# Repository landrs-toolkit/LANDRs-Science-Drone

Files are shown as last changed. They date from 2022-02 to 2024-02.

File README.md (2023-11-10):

# Nyala HexaQuad

<a href="https://github.com/landrs-toolkit/LANDRs-Science-Drone">
         
 </a>

LogoDiagram

**Welcome to the primary source for all the design materials and users guides for the LANDRS Nyala HexaQuad.**

The HexaQuad is an open source, modular multirotor designed with stringent academic research data provenance in mind.
It is a simple to replicate, user friendly design for drone novices and experts alike, all you need are some basic tools, a 3D printer and once off access to CNC routing.

**Specifications:**
* 15-20 minutes operation time with 1-3kg payload
* Configured as Hex or Quad
* Max flight time: 30 - 35 minutes (16.8Ah)
* Max Payload: 2kg(Quad); 5kg(Hex)
* Battery Voltage: 6S

A short description of the HexaQuad can be found on YouTube [here](https://youtu.be/huQ6nF6V_Ks) and detailed specifications can be seen below.

## Documentation

The documentation can be found at [https://www.landrs.org/LANDRs-Science-Drone/](https://www.landrs.org/LANDRs-Science-Drone/). This will house the build instructions, assistance guides and all information relating to the HexaQuad.

## Presentation at Linux Open Source Summit Europe 2022
We were invited to present our work at the Linux Open Source Summit that took place in Dublin, 2022. The Linux foundation flew us out to present our work to the open source community.

The full presentation given at the summit can be found on YouTube [here](https://youtu.be/drAO9xs3WeU).

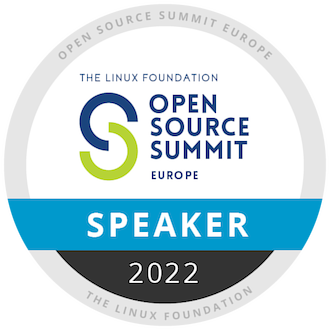
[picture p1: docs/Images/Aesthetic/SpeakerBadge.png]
LogoDiagram


In the presentation we explore the motivation for the HexaQuad and how it can benefit researchers compared to drones available off the shelf. There is further exploration of the design considerations and performance.

## License
Licensed under [CERN-OHL-P v2](https://cern.ch/cern-ohl) permissive variant or later.

## Citation
If using the work presented here, please use one of the following citation:

> **APA**: Borrageiro, M. G., & Wyngaard, J. Nyala HexaQuad, LANDRs' Science Drone (Version 1.0.0) [Designs]. https://github.com/landrs-toolkit/LANDRs-Science-Drone

> **BibTex**: @misc{Borrageiro_Nyala_HexaQuad_LANDRs,
author = {Borrageiro, Mauro Giovanni and Wyngaard, Jane},
title = {{Nyala HexaQuad, LANDRs' Science Drone}},
url = {https://github.com/landrs-toolkit/LANDRs-Science-Drone}
}

## Detailed Specifications:
| **Model** | **General** |
|---|---|
| Flight Controller | Cubepilot Orange Cube |
| Autopilot | Arducopter 4.3.1 |
| Navigation | Here 2 GPS |
| Remote Control | FrSky Archer GR8 ACCESS (Receiver), Taranis Q X7S (Transmitter) |
| Telemetry Radio | RFD900+ 900MHz radios |
| Operating Range (km) | 2 |
| Battery Voltage (V) | 22.2 (3.7x6) |
| Battery Capacity (Ah) | 8.4 - 16.8 |
| Motor | T-Motor MN5008 340KV 6S |
| Propeller | T-Motor P18x6.1 Carbon Fiber |
| Wingspan (mm) | 1120 (no props), 1578 (props on) |
| | **Hexacopter** |
| Configuration | Hex-X |
| Dimensions (W x L x H mm) | 1120 x 970 x 450 |
| Frame Weight (kg) | 2.7 |
| AUW, No battery (kg) | 3.7 |
| AUW(kg) | 4.6 - 5.5 |
| Max Thrust (N) | 246 |
| Max Payload (kg) | 5 |
| Typical Flight Time (1kg, min) | 28.8 |
| Maximum Flight Time (min) | 19.2 - 30.6 |
| | **Quadcopter** |
| Configuration | Quad-X |
| Dimensions (W x L x H mm) | 792 x 792 x 450 |
| Frame Weight (kg) | 2.2 |
| AUW, No battery (kg) | 2.9 |
| AUW(kg) | 3.8 - 4.6 |
| Max Thrust (N) | 165 |
| Max Payload (kg) | 2 |
| Maximum Flight Time, single battery (min) | 23 |

## Contact Details
You can connect with me on LinkedIn or via Email:

[Mauro-Borrageiro-87a5131b5](https://www.linkedin.com/in/mauro-borrageiro-87a5131b5/)

[mauro.borrageiro7@gmail.com](mauro.borrageiro7@gmail.com)

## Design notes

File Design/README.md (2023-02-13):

# Nyala HexaQuad Design Files

<a href="https://github.com/landrs-toolkit/LANDRs-Science-Drone/blob/main/docs/Images/Aesthetic/HexaQuadTracing.jpg">
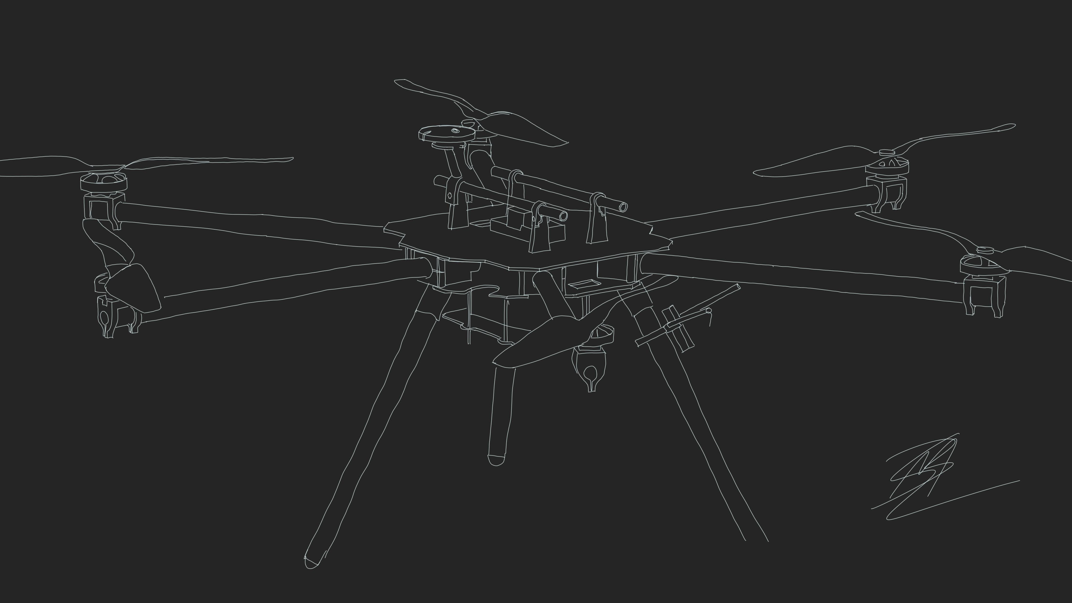
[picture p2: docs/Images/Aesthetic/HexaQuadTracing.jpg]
3DPrintBanner
         
 </a>

This folder contains all the mechanical 3D part files for the Nyala HexaQuad which can be editted and iterated. Included are the files for printing and CNC routing to recreate prototype 1 (Release 2022).

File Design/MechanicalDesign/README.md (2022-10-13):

# Mechanical Design Files for the LANDRs Science Drone

## Quad Configuration Part List:
*Note this is a minimal list and will be updated to the full requirements in November 2022*

| Part Name | Quantity | Manufacturing Technique |
|---|---|---|
| [BatteryPlate](https://github.com/landrs-toolkit/LANDRs-Science-Drone/tree/main/Design/MechanicalDesign/BatteryPlate) | 1 | CNC Carbon Fiber |
| [WingNutExtender](https://github.com/landrs-toolkit/LANDRs-Science-Drone/tree/main/Design/MechanicalDesign/BatteryPlate) | 4 | 3D Print |
| [CenterHub Top](https://github.com/landrs-toolkit/LANDRs-Science-Drone/tree/main/Design/MechanicalDesign/CenterHubs/TopPlate) | 1 | CNC Carbon Fiber |
| [CenterHub Bot](https://github.com/landrs-toolkit/LANDRs-Science-Drone/tree/main/Design/MechanicalDesign/CenterHubs/BottomPlate) | 1 | CNC Carbon Fiber |
| [LandingGearTubeCap](https://github.com/landrs-toolkit/LANDRs-Science-Drone/tree/main/Design/MechanicalDesign/LandingGear)  | 4 | 3D Print |
| [RotorBoomMounts Top](https://github.com/landrs-toolkit/LANDRs-Science-Drone/tree/main/Design/MechanicalDesign/RotorBoomMounts) | 4 | 3D Print |
| [RotorBoomMounts Bot](https://github.com/landrs-toolkit/LANDRs-Science-Drone/tree/main/Design/MechanicalDesign/RotorBoomMounts/NutInsert) | 4 | 3D Print |
| [MotorMounts](https://github.com/landrs-toolkit/LANDRs-Science-Drone/tree/main/Design/MechanicalDesign/MotorMounts) | 4 | 3D Print |
| [TopRail](https://github.com/landrs-toolkit/LANDRs-Science-Drone/tree/main/Design/MechanicalDesign/RailMounting) | 4 | 3D Print |
| [GPSMount](https://github.com/landrs-toolkit/LANDRs-Science-Drone/tree/main/Design/MechanicalDesign/GPSMounts) | 1 | 3D Print |
| [PDBMount](https://github.com/landrs-toolkit/LANDRs-Science-Drone/tree/main/Design/MechanicalDesign/PDBMount) | 1 | 3D Print |
| [NiTubeMounting](https://github.com/landrs-toolkit/LANDRs-Science-Drone/tree/main/Design/MechanicalDesign/SensorMounts/NiTubeMounting) | 2 | 3D Print |
| [RC Receiver](https://github.com/landrs-toolkit/LANDRs-Science-Drone/tree/main/Design/MechanicalDesign/RadioReceivers) | 1 | 3D Print |
| [Telemetry Radio](https://github.com/landrs-toolkit/LANDRs-Science-Drone/tree/main/Design/MechanicalDesign/RadioReceivers) | 1 | 3D Print |

## Print Guide
*For assistance with printing, please consult the HexaQuad dedicated documentation [here](https://www.landrs.org/LANDRs-Science-Drone/)*

- [Print Orientations](https://www.landrs.org/LANDRs-Science-Drone/GettingStarted/BuildInstructions/PrintGuide.html)
- [Nut Inserts](https://www.landrs.org/LANDRs-Science-Drone/GettingStarted/Tutorials/3DPrintInserts.html)

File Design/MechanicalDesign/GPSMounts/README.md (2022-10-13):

# GPS Mounting
This folder contians the development of the GPS mount. Two version were tested, a short and long option. The short mount is currently in use.

## All in One Mount
_This is the current prototype being used on both the Quad and Hex configuration of the multirotor._

<a href="https://github.com/landrs-toolkit/LANDRs-Science-Drone/blob/main/Design/MechanicalDesign/GPSMounts">
         
 </a>
<a href="https://github.com/landrs-toolkit/LANDRs-Science-Drone/blob/main/Design/MechanicalDesign/GPSMounts/Ai1HEREGpsMount.STL">
         
 </a>

This revision combined the rail mount and base plate into one single 3D print. Previously, these two components were seperate for ease of printing however,
 they were connected by a steel bolt. This was causing interference with the compass.
 
 There are two revisions of the Ai1HereGPSMount:
 - Ai1HereGpsMount (_Current Prototype (06/01/2022)_)
   - [STL File](https://github.com/landrs-toolkit/LANDRs-Science-Drone/blob/main/MechanicalDesign/GPSMounts/Ai1HEREGpsMount.STL), [SOLIDWORKS Part](https://github.com/landrs-toolkit/LANDRs-Science-Drone/blob/main/MechanicalDesign/GPSMounts/Ai1HEREGpsMount.SLDASM)
 - Ai1HereGpsMountLong
   - [STL File](https://github.com/landrs-toolkit/LANDRs-Science-Drone/blob/main/MechanicalDesign/GPSMounts/Ai1HEREGpsMountLong.STL), [SOLIDWORKS Part](https://github.com/landrs-toolkit/LANDRs-Science-Drone/blob/main/MechanicalDesign/GPSMounts/Ai1HEREGpsMountLong.SLDASM)
 
 The difference is a longer stem on the _long_ version to increase the height of the GPS from the center hub.

# Blank Designs for Customisation

## GPS Rail Mount
The GPS rail mount is still being used to connect the GPS to the top rails, it has simply been incorporated into a single 3D printed part in the Ai1HereGpsMount.

## HERE GPS
This was an attempt to create a snap-fit joint to hold he GPS in place. This is designed to work with the HERE GPS units, howevere requries some revision
and improvement to work as intended.

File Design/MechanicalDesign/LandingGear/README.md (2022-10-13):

# Landing Gear
This folder contains the current supported landing gear designs.

## Simple Tripod
<a href="https://github.com/landrs-toolkit/LANDRs-Science-Drone/tree/main/Design/MechanicalDesign/LandingGear/SimpleTripod">
         
 </a>
 <a href="https://github.com/landrs-toolkit/LANDRs-Science-Drone/blob/main/Design/MechanicalDesign/LandingGear/SimpleTripod/LGTubeCap.STL">
         
 </a>

This design makes use of simple tripod design for the landing gear. This steers away from the common 'T-Shaped' landing gear that has become synonymous with sUAS.
The Design is comprised of a carbon fiber tube which connects to the [Rotor Boom Mounts](https://github.com/landrs-toolkit/LANDRs-Science-Drone/tree/main/Design/MechanicalDesign/RotorBoomMounts) and has a simple rounded end that comes into contact 
with the floor. This is part is known as a [Landing Gear Tube Cap](https://github.com/landrs-toolkit/LANDRs-Science-Drone/tree/main/Design/MechanicalDesign/LandingGear/SimpleTripod) and is 3D printed.

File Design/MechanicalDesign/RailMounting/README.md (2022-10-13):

# Gimbal Rail Mounts
This folder contains the mounts to support the top and bottom gimbal rails. Both rails are a 250mm long carbon fiber tube with a 12mm diameter.

## Top Gimbal Rail Mount:
<a href="https://github.com/landrs-toolkit/LANDRs-Science-Drone/blob/main/Design/MechanicalDesign/RailMounting/TopRail/PrtTopGimbalNutInsert.STL">
         
 </a>
<a href="https://www.landrs.org/LANDRs-Science-Drone/GettingStarted/Tutorials/3DPrintInserts.html">
         
 </a>

This folder contains the top gimbal rail mounting part. Included is a PDF drawing with dimentions to aid with custom mounting. [Top Rail](https://github.com/landrs-toolkit/LANDRs-Science-Drone/tree/main/Design/MechanicalDesign/RailMounting/TopRail)

## Bottom Gimbal Rail Mount:
<a href="https://github.com/landrs-toolkit/LANDRs-Science-Drone/tree/main/Design/MechanicalDesign/RailMounting/BotRail/TRodGimbalMountNutInsert.STL">
         
 </a>
<a href="https://www.landrs.org/LANDRs-Science-Drone/GettingStarted/Tutorials/3DPrintInserts.html">
         
 </a>

This folder contains the bottom gimbal rail mounting part. Included is a PDF drawing with dimentions to aid with custom mounting. [Bot Rail](https://github.com/landrs-toolkit/LANDRs-Science-Drone/tree/main/Design/MechanicalDesign/RailMounting/TopRail)

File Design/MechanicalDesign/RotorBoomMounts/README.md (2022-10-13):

# Rotorboom Mounts

The Rotorboom Mounts assist in two ways, firstly to connect the rotorbooms (arms) of the HexaQuad to the central hub of the drone. Secondly, they provide an attachment point for the landing gear to the central hub.

Thus there are two configurations this doc covers: a rotorboom mount that accommodates the landing gear and the rotorboom; and a configuration that accommodates the rotorboom only.

# Mounts Differences

## Top Rotorboom Mount
<a href="https://github.com/landrs-toolkit/LANDRs-Science-Drone/blob/main/Design/MechanicalDesign/RotorBoomMounts/NutInsert/LGLegMountTopV3.2NutInsert.STL">
         
 </a>
 <a href="https://www.landrs.org/LANDRs-Science-Drone/GettingStarted/Tutorials/3DPrintInserts.html">
         
 </a>

The top mount is used in both configurations, that accommodating the landing gear and the rotorboom only.

## Bottom Rotorboom Mount

<a href="https://github.com/landrs-toolkit/LANDRs-Science-Drone/blob/main/Design/MechanicalDesign/RotorBoomMounts/LGLegMountBotV3.1.STL">
         
 </a>

The bottom mount is used only in the case when landing gear is required to be attached to the rotorboom.

# Configurations

## Rotorboom Only
This configuration onlt requires the top mount.

**Required 3D prints:**

- 2 x [LGLegTopMount](https://github.com/landrs-toolkit/LANDRs-Science-Drone/blob/main/Design/MechanicalDesign/RotorBoomMounts/NutInsert/LGLegMountTopV3.2NutInsert.STL)

**Illustration:**

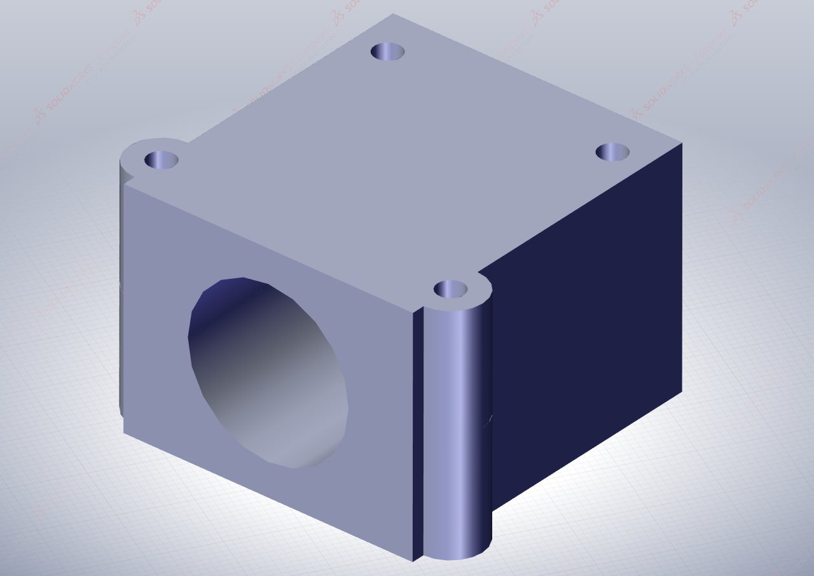
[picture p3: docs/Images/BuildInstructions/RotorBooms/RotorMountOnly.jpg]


## Rotorboom and Landing Gear

This configuration makes use of both the top and bottom mounts.

**Required 3D prints:**

- 1 x [LGLegTopMount](https://github.com/landrs-toolkit/LANDRs-Science-Drone/blob/main/Design/MechanicalDesign/RotorBoomMounts/NutInsert/LGLegMountTopV3.2NutInsert.STL)
- 1 x [LGLegBotMount](https://github.com/landrs-toolkit/LANDRs-Science-Drone/blob/main/Design/MechanicalDesign/RotorBoomMounts/LGLegMountBotV3.1.STL)

**Illustration:**

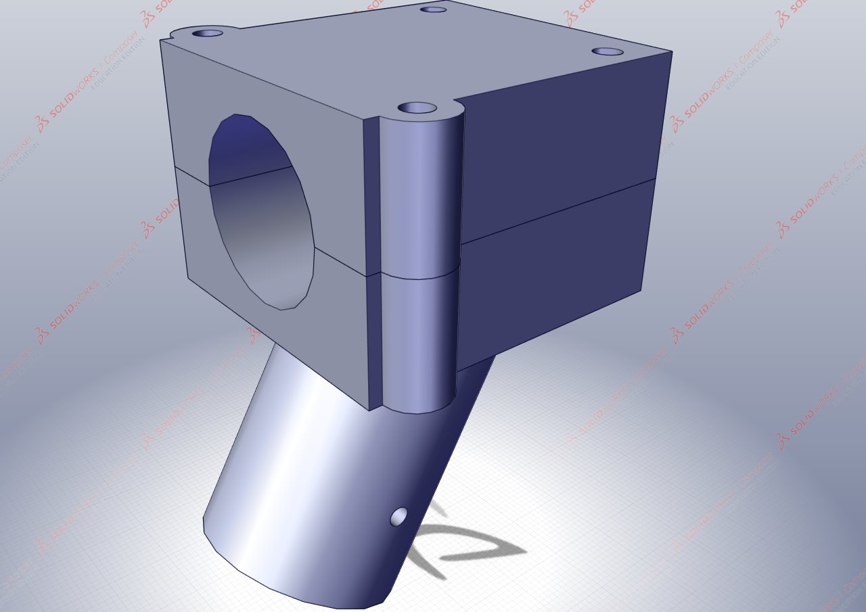
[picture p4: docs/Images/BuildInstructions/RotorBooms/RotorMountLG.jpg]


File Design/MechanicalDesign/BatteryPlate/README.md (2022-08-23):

# Battery Mounting
This repositorty contains the battery mounting plate that connects to the center hub. This design is being prototyped and is likely to have some minor updates to improve operation.

## Battery Plate with Butterfly Nut

<a href="https://github.com/landrs-toolkit/LANDRs-Science-Drone/blob/main/Design/MechanicalDesign/BatteryPlate">
         
 </a>
<a href="https://github.com/landrs-toolkit/LANDRs-Science-Drone/blob/main/Design/MechanicalDesign/BatteryPlate/BatPlateBtFlyNut.DXF">
         
 </a>

The contents of the folder:

**BatPlateButFlyNut.SLDPRT**:
- SOLIDWORKS, 3D editable part file of the battery mounting plate secured with butterfly nuts.

**BatPlateButFlyNut.DXF**:
- CNC Cutting/Routing file for the battery plate.
- The material used in the prototype was Carbon Fiber Twill Weave, 3mm thickness.

**WingNutExtender.SLDPRT**

<a href="https://github.com/landrs-toolkit/LANDRs-Science-Drone/blob/main/Design/MechanicalDesign/BatteryPlate/WingNutExtender.SLT">
         
 </a>
 <a href="https://www.landrs.org/LANDRs-Science-Drone/GettingStarted/Tutorials/3DPrintInserts.html">
         
 </a>

- SOLIDWORKS, 3D editable part file for a printable wingnut to assist with securing the battery. This part requires an embedded M5 nut.

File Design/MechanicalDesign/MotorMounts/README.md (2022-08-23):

# 3D Printed Motor Mounts
The Science Drone is making use of 3D printed motor mounts. Motor mounts can often be complex shapes and thus make the manufacturing process somewhat difficult and long. 3D printing fixes this problem and shortens the manufacturing process.

There was a concern of strength of the 3D printed materials. Thus a Tensile loading test was performed on two materials to investigate if either would be sufficient for the purpose. Both materials proved suitable interms of strength however, concerns of temperature and melting points of the materials was raised. PETG has a higher melt temperature compared to PLA and this partially motivated the comparison between the two materials. Fortunately, it was found during testing that the motor operating temperatures were not a concern and thus the material with a higher tensile strength was used, PLA.

The Motor Mount went through three significant design iterations and are listed below.
The folder contains 3D `.STL` files for printing and `.SLDPRT` SOLIDWORKS editable part files

 <a href="https://github.com/landrs-toolkit/LANDRs-Science-Drone/blob/main/Design/MechanicalDesign/MotorMounts/MMPrintV1.3c.STL">
         
 </a>
 
## MotorMount Print (MMPrint):
-  A simple design with a single securing point to mount the motor to the rotor boom.

**Design Concerns:**
1.   The mount had to be aligned to the end of the rotor boom and then also leveled. 
2.   If the single securing point came undone or failed, then the motor would certainly fall off and cause more damage.

These issues were revised in iteration 2.

## MMPrintV1.2:
- Iteration 2 saw the addition of an end stopper plate to help align the motor mount with the end of the rotor boom. 
- There was also an additional securing point for redundancy but also to further secure the motor mount to the rotor boom.

**Design Concerns:**
1. The design of the securing point was a point subject to high strain when loaded to fasten the mount to the rotor boom. Due to the sharp corner and contant width, this resulted in a high stress point and broke under loading.
2. The tolerance of the rotorboom hole was upped by 0.3mm to account for the error in 3D printing. [ID change: 25mm->25.3mm]

## MMPrintV1.3:
- Iteration 3 introduced more tolerance in the diameters to account for 3D printing error. 
- A Fillet was added to the design to distribute the stress more evenly along the securing point.
- The thickness of the mount was increased by 1mm as a precaution and avoid another iteration.
- Added a angled slot to accommodate the motor wires. This allows the wires to go further into the rotor boom instead of being exteranl to the boom.

**Design Concerns:**
1. The bottom of the motor shaft seems to be touching the top of the motor mount, adding friction and making it more difficult to turn the motor. [Proposed to add a cut out for clearance]

## MMPrintV1.4:
<a href="https://github.com/landrs-toolkit/LANDRs-Science-Drone/blob/main/Design/MechanicalDesign/MotorMounts">
         
 </a>

- Added a clearance cut to the surface where the motor shaft was touching.

**Design Notes:**
The concern raised in the previous version was proved true. The bottom of the motor shafts were rubbing on the 3D print, wearing away the material. The clearance was added as a precaution to prevent unnecessary added friction on the motor shafts.

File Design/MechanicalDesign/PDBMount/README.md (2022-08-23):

# Power Distribution Board (PDB) Mount:
<a href="https://github.com/landrs-toolkit/LANDRs-Science-Drone/blob/main/Design/MechanicalDesign/PDBMount/PDBMount.STL">
         
 </a>
 <a href="https://www.landrs.org/LANDRs-Science-Drone/GettingStarted/Tutorials/3DPrintInserts.html">
         
 </a>

The PDB mount is designed for the [Matek PDB-HEX, 12S](https://www.mateksys.com/?portfolio=pdb-hex) board. The simple mount is to secure the PDB and provide some electrical isolation of the PCB from the carbon fiber center plate. 

The design mirrors the shape of the PCB and has embedded nuts to secure the PDB to the mount. The PDB is currently secured to the center hub with industrial velcro.

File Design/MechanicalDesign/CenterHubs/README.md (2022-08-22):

# Modular Chassis Unit (MCU) Designs
This folder contains the part and CNC routing files for the Top and Bottom plates of the centeral hub.

Simulation studies were performed on the centeral hub designs listed below. The simulation studies were instrumental in determining which set of plates would best suit the applications of the multirotor.

## DoDeca Chassis Unit, Design 1
The DoDeca design is based off a polygon with 12 sides (a dodecagon). 
This number of sides allowed for a satisfying mounting configuration of the rotors booms for both a quad and hex configuration. 
12 sides mean that in either a quad or hex configuration the rotor booms would always be perpendicular to a chassis edge.

This is a simple design and increases in surface area equally in all directions. Weight minimizing cutouts can be added in to imporve weight to strength performance.

## Oblong Chassis Unit, Design 2
The Oblong design is a more rectangular based design where the majority of the surface area is focused along one axis. 
The resulting shape is a chassis plate extending longer in one axis compared to its relative perpendicular axis. An example can be seen in the following figure:


## Double Plate Unit, Design 3
<a href="https://github.com/landrs-toolkit/LANDRs-Science-Drone/blob/main/Design/MechanicalDesign/CenterHubs">
         
 </a>

The following ietration builds on the ideas in the previous versions. This design contains a top and bottom plate that "sandwiches" the Rotor-leg mounts for added support and structural strength. The bottom plate has various cutouts to accommodate the reconfiguration between Hex and Quad, leading to the interchangable HexaQuad.

**CHObDoubleTop:** 
- Top plate of the central hub.

**CHDoDeDoubleBot:** 
- Bottom plate of the central hub.

### Version 1.2

The files for version 1.2 can be found in the following folders:
- [TopPlate](https://github.com/landrs-toolkit/LANDRs-Science-Drone/tree/main/Design/MechanicalDesign/CenterHubs/TopPlate)
- [BottomPlate](https://github.com/landrs-toolkit/LANDRs-Science-Drone/tree/main/Design/MechanicalDesign/CenterHubs/BottomPlate)

Each folder contains an editable 3D SOLIDWORKS file and a non-editable DXF file used for CNC cutting/routing of the plates.

### Visual Representation Only:
[This folder](https://github.com/MBorrageiro/cad-drawings/tree/main/CenterHub/MCUDesigns/STLs) contains STL files of certain assemblies and parts just to serve as a visual representation. It is not the intention for these parts to be 3D printed.

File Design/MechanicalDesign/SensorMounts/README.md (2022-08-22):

# Sensor Mounts and Related Items
*Under development...*

This folder contains parts to assist with mounting sensors to the HexaQuad. It also provides solutions for mounting items associated with sensors such as Type-C USB sockets for powering devices.

## Type-C Socket Mounts:
Some suggested and tested mounting strategies for USB Type-C sockets for powering devices. [Type-C Mounts](https://github.com/landrs-toolkit/LANDRs-Science-Drone/tree/main/Design/MechanicalDesign/SensorMounts/C-TypeSocketMounts)

## Nut Insert (Ni) Tube Mounting:
A simple mount that fits onto any 25mm diameter carbon tube of the HexaQuad. This is used for mounting the RFD telemetry radios and R/C receiver. [Ni-Tube Mount](https://github.com/landrs-toolkit/LANDRs-Science-Drone/tree/main/Design/MechanicalDesign/SensorMounts/NiTubeMounting)

## Nut Insert (Ni) Rail Mounting:
A simple mount to aid connection to the gimbal rails. This part has a 12mm diameter and can be used on either the top or bot gimbal rail. [Ni-Rail Mount](https://github.com/landrs-toolkit/LANDRs-Science-Drone/tree/main/Design/MechanicalDesign/SensorMounts/NutInsertRailMounting)

## Rail Snap On Mounts:
A horrizontal bar that 'snap-locks' onto the parallel 12mm gimbal rails. There are two lengths available due to different spacings of the top and bot gimbal rails. [SnO Mounts](https://github.com/landrs-toolkit/LANDRs-Science-Drone/tree/main/Design/MechanicalDesign/SensorMounts/RailSnapMount)

## Rail Mounting Blanks:
This folder contains blank models of the GPS rail mount and gimbal rail mounts. These blanks can be merged with custom sensor mounts to connect them to the HexaQuad. [Rail Mounting Blanks](https://github.com/landrs-toolkit/LANDRs-Science-Drone/tree/main/Design/MechanicalDesign/SensorMounts/RailMountingBlanks)

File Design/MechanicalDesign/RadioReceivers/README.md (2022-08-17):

# Radio Receiver Mounts
This folder contains mounting designs for the radio controller (R/C) and the telemetry recievers. These mounts are not strickly necessary and can be replaced with 3M or other adhessive options, however this is not recommended.

## RC Reciever:
 <a href="https://github.com/landrs-toolkit/LANDRs-Science-Drone/blob/main/Design/MechanicalDesign/RadioReceivers/RCReceiver">
         
 </a>

The R/C designs are specificly for the FrSky ARCHER GR8 Receiver.
There are two designs inlcuded, where the antenna are oriented 90&deg; apart, just in two different planes. This snap fit makes use of the following [carbon fiber tube mount](https://github.com/landrs-toolkit/LANDRs-Science-Drone/tree/main/Design/MechanicalDesign/SensorMounts/NiTubeMounting)

**90VP:**

The antenna are 90&deg; apart in the vertical plane(VP). One runs vertically and the other horizontally.

**90HP:**

This differs to the VP in that both antenna are in the horizotnal plane(HP), yet still 90&deg; apart.

## Telemetry Radios.
 <a href="https://github.com/landrs-toolkit/LANDRs-Science-Drone/blob/main/Design/MechanicalDesign/RadioReceivers/TelemetryRadios">
         
 </a>

The HexaQuad has two options for telemetry links, one makes use of RFD900 radios and the second, is based on a mobile network. The telemetry links are the main connection between the HexaQuad and the ground control station(GCS). The suggested mounting options are listed below:

### RFD900 Mounts:
There are two differnet 3D printable cases, one that allows mounting of the receiver on the HexaQuad and another that serves as a protective case of the transmitter that connects to the GCS.

**Telemetry Case for HexaQuad:**

A simple snap fit case to protect the RFD telemetry radio and provide a mounting point to secure the radio to the HexaQuad. This snap fit makes use of the following [carbon fiber tube mount](https://github.com/landrs-toolkit/LANDRs-Science-Drone/tree/main/Design/MechanicalDesign/SensorMounts/NiTubeMounting)

[STL Files](https://github.com/landrs-toolkit/LANDRs-Science-Drone/blob/main/Design/MechanicalDesign/RadioReceivers/TelemetryRadios)

**Telemetry Case for GCS:**

*Coming soon...*

## 5G Mobile Network Mounts:
*Coming soon...*

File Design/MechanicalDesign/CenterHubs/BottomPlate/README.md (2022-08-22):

# Center Hub Dodecagon Bottom Plate
<a href="https://github.com/landrs-toolkit/LANDRs-Science-Drone/blob/main/Design/MechanicalDesign/CenterHubs/BottomPlate/CHDoDeDoubleBotV1.2.DXF">
         
 </a>

The bottom plate of the LANDRs Hex and Quad drone. The plate has universal cuts that allow the sUAS to be changed between a hexacopter or a quadcopter.

This folder contains the following files:

**CHDoDeDoubleBotV1.2.SLDPRT:**
- Solidworks Editable 3D file.
- The dimensions of the plate can be altered or features can be added or removed.

**CHDoDeDoubleBotV1.2.DXF:**
- The DXF file is used for CNC cutting of the plate.

NOTE: It is recommended to use the Solidworks Part File to export the part to different formats if required.

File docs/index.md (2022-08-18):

---
layout: default
title: Home
nav_order: 1
---

# Nyala HexaQuad Documentation
Welcome to the "landing ;)" page of the HexaQuad, LANDRs Modular Science Multicopter.
This is the home of the NyHQ's Documentation and will guide you through assembly, debugging and hopefully some customisation. 



<a href="https://github.com/landrs-toolkit/LANDRs-Science-Drone/blob/main/docs/Images/Aesthetic/HexaQuadTracing.jpg">
         3DPrintBanner
 </a>

**Status:**
* The HexaQuad is undergoing performance testing, see provisional flight performance [here](https://youtu.be/huQ6nF6V_Ks)
* Repo currently primarily contains CAD Drawings related to the 3D printable parts and CNC'd parts.
* This repo intends to release version 1 before the end of 2022

**License**
Licensed under [CERN-OHL-P v2](https://cern.ch/cern-ohl) permissive bariant or later.

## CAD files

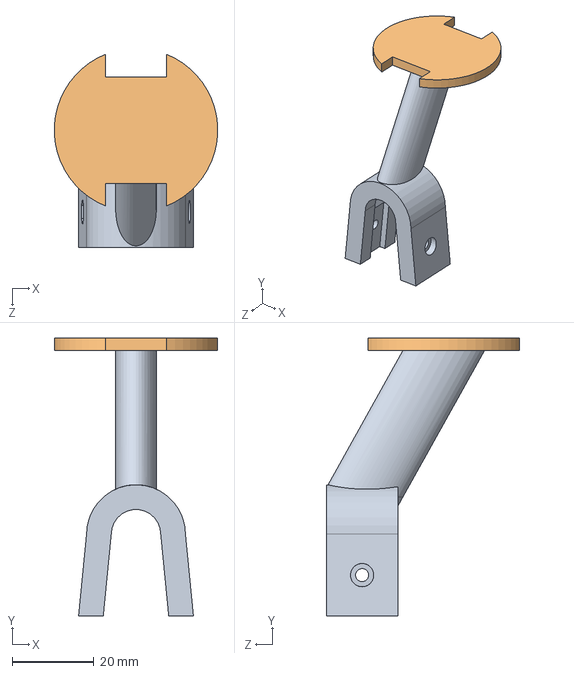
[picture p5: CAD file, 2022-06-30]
Design/MechanicalDesign/GPSMounts/Ai1HEREGpsMount.SLDASM
39.9 x 68.0 x 47.3 mm
GpsRailMount
HEREGpsBSimple

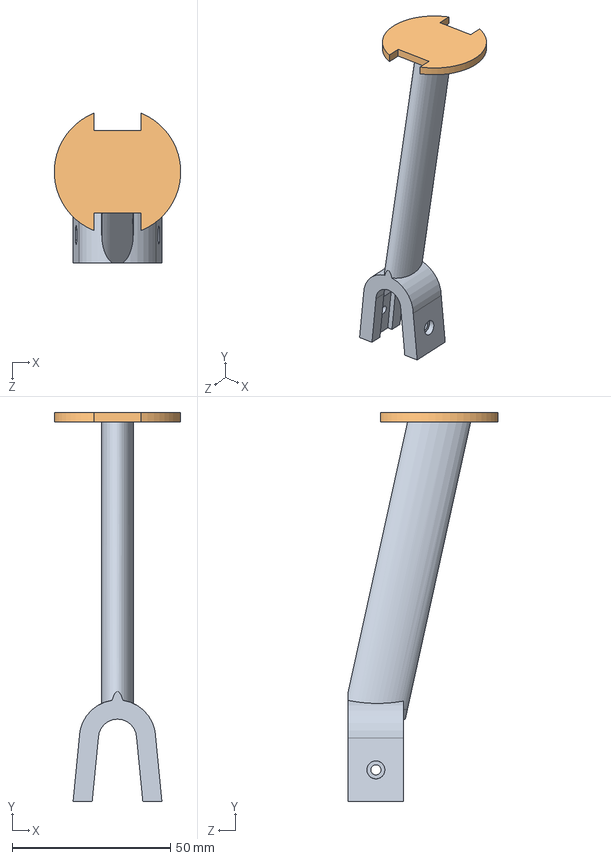
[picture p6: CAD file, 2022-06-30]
Design/MechanicalDesign/GPSMounts/Ai1HEREGpsMountLong.SLDASM
39.9 x 123.0 x 47.3 mm
GpsRailMountLong
HEREGpsBSimple

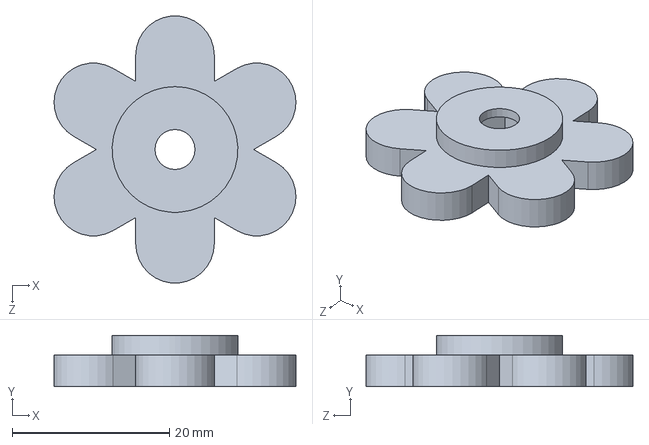
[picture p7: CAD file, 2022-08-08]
Design/MechanicalDesign/BatteryPlate/WingNutExtender.SLDPRT
30.8 x 6.50 x 33.9 mm

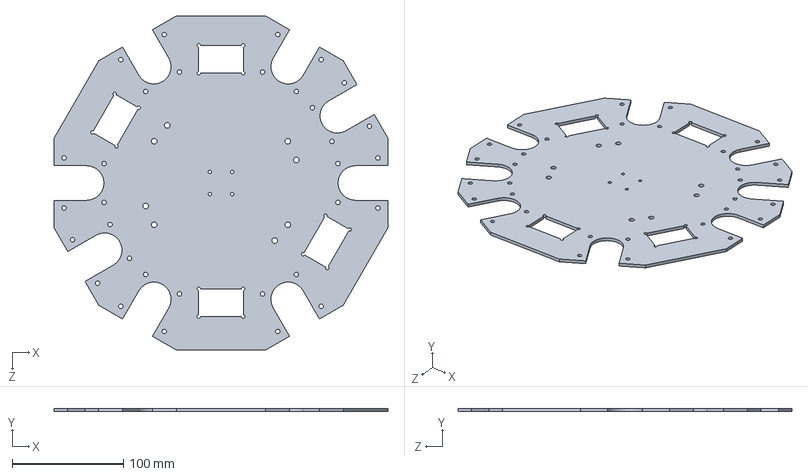
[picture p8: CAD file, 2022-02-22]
Design/MechanicalDesign/CenterHubs/BottomPlate/CHDoDeDoubleBotV1.2.SLDPRT
300.0 x 3.00 x 300.0 mm

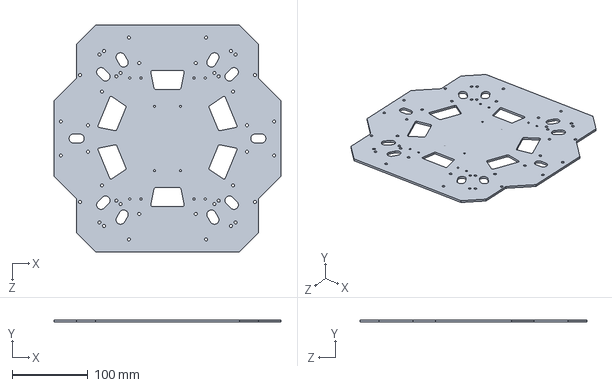
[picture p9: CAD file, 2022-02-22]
Design/MechanicalDesign/CenterHubs/TopPlate/CHObDoubleTopV1.2.SLDPRT
300.0 x 3.00 x 300.0 mm

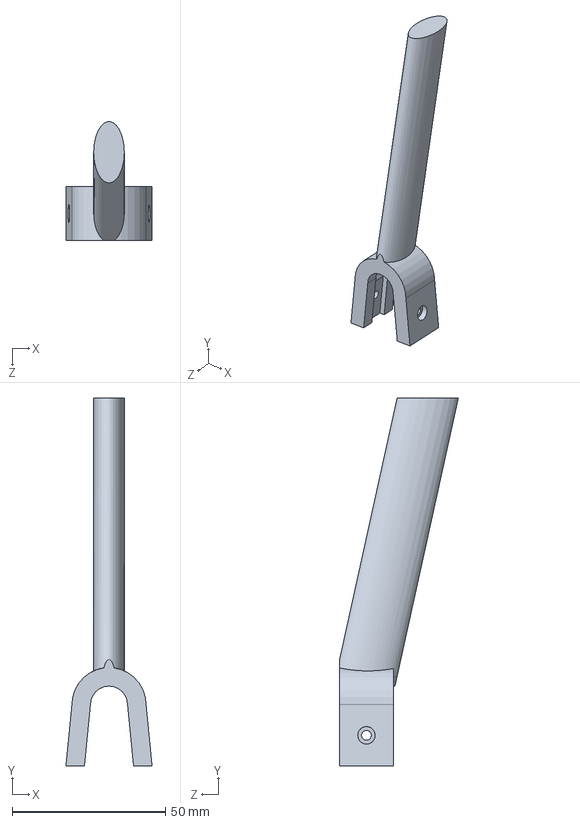
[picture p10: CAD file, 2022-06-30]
Design/MechanicalDesign/GPSMounts/GpsRailMount.SLDPRT
28.1 x 120.0 x 38.7 mm

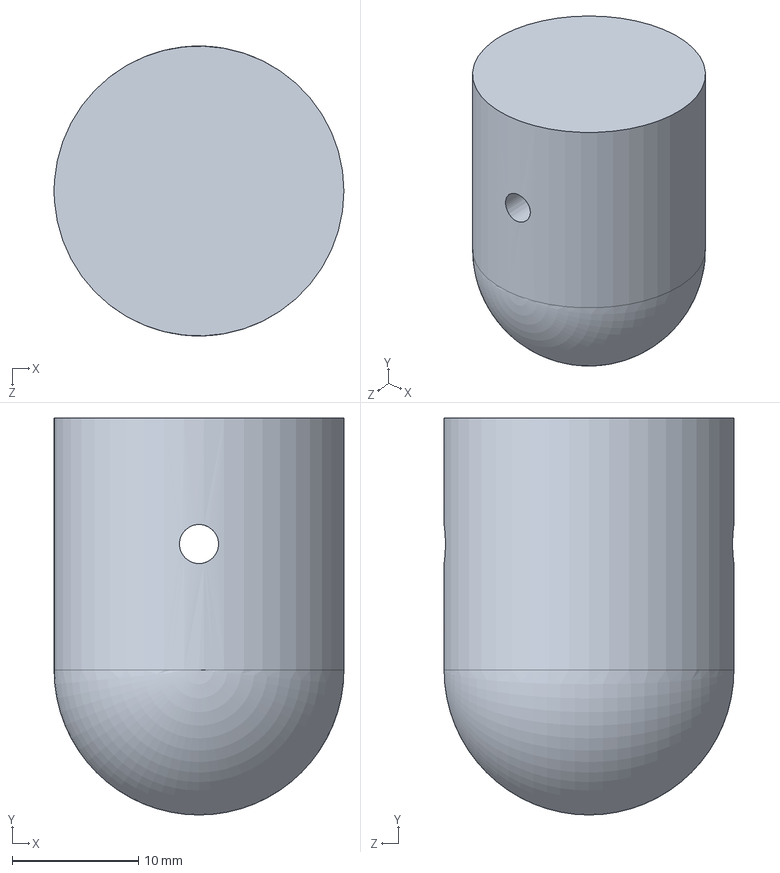
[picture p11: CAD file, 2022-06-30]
Design/MechanicalDesign/LandingGear/SimpleTripod/LGTubeCap.SLDPRT
23.0 x 31.5 x 23.0 mm

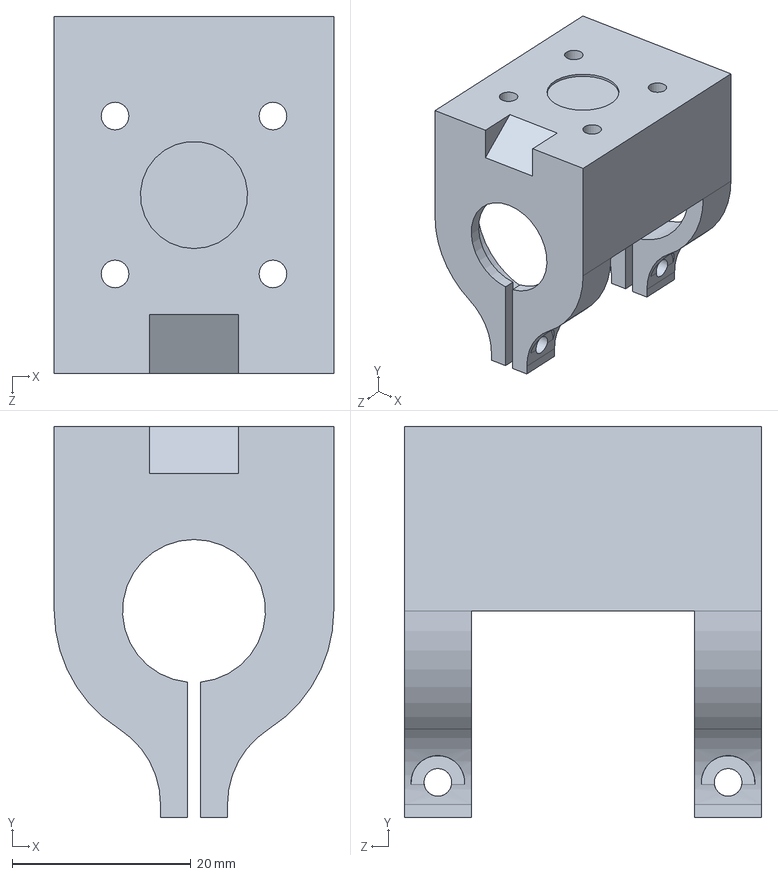
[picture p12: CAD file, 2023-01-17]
Design/MechanicalDesign/MotorMounts/MMPrintV1.5.SLDPRT
31.3 x 43.8 x 40.0 mm

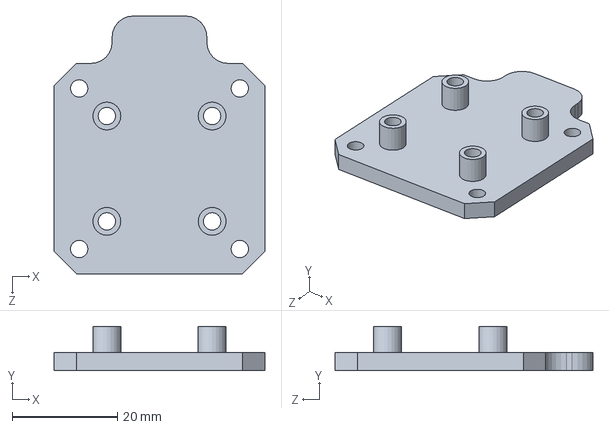
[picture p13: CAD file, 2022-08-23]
Design/MechanicalDesign/PDBMount/PDBMount.SLDPRT
40.0 x 8.40 x 49.0 mm

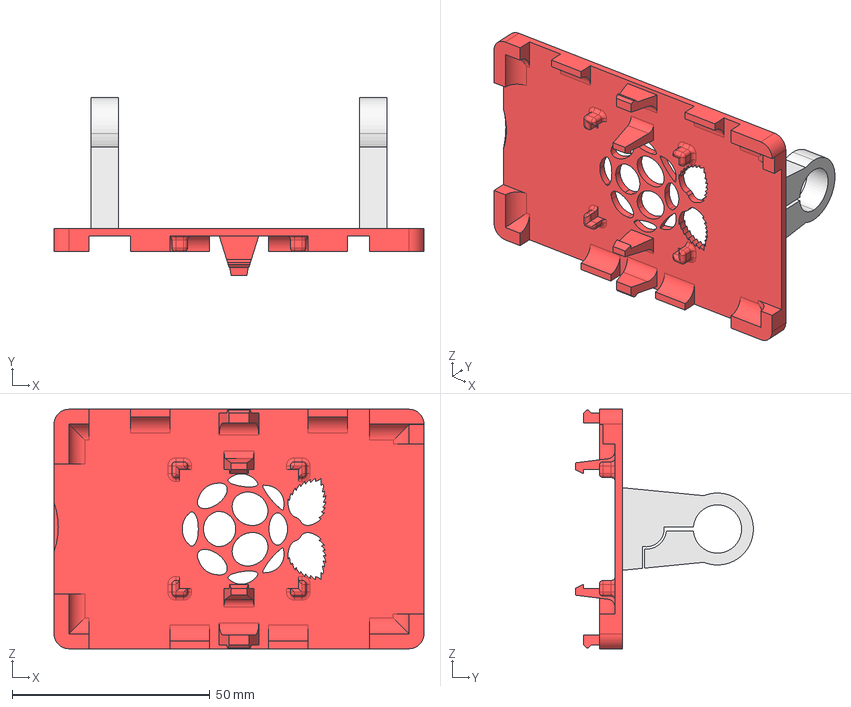
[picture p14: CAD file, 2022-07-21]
Design/MechanicalDesign/Pi4Case/Lid_WithMounts.FCStd
93.6 x 45.0 x 60.6 mm
Lid
RailMountBlank
RailMountBlank001

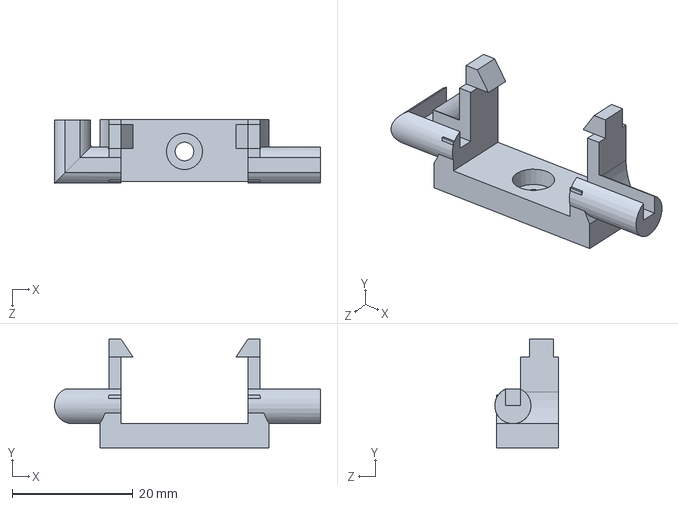
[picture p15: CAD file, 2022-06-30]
Design/MechanicalDesign/RadioReceivers/RCReceiver/FrSkyMount90VP.SLDPRT
44.0 x 18.0 x 10.5 mm

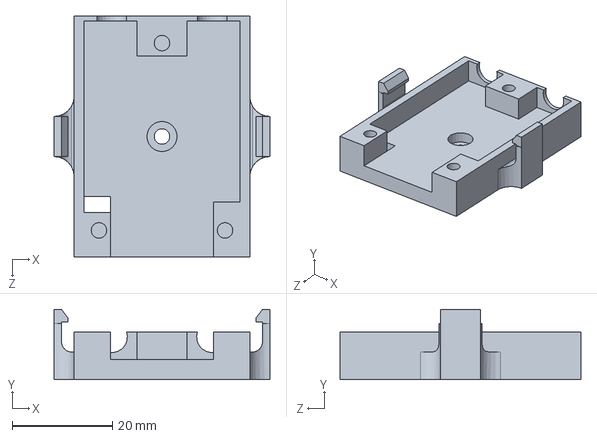
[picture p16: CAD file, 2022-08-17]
Design/MechanicalDesign/RadioReceivers/TelemetryRadios/RFDBotCoverSnapFit.SLDPRT
43.0 x 14.0 x 48.0 mm

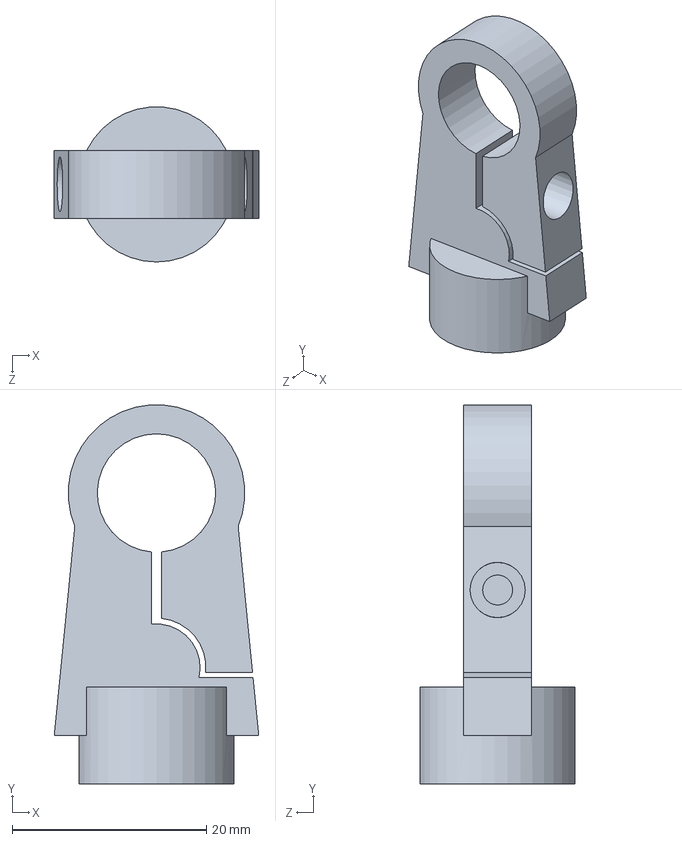
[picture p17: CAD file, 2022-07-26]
Design/MechanicalDesign/RailMounting/BotRail/TRodGimbalMountNutInsert.SLDPRT
21.1 x 39.1 x 16.0 mm

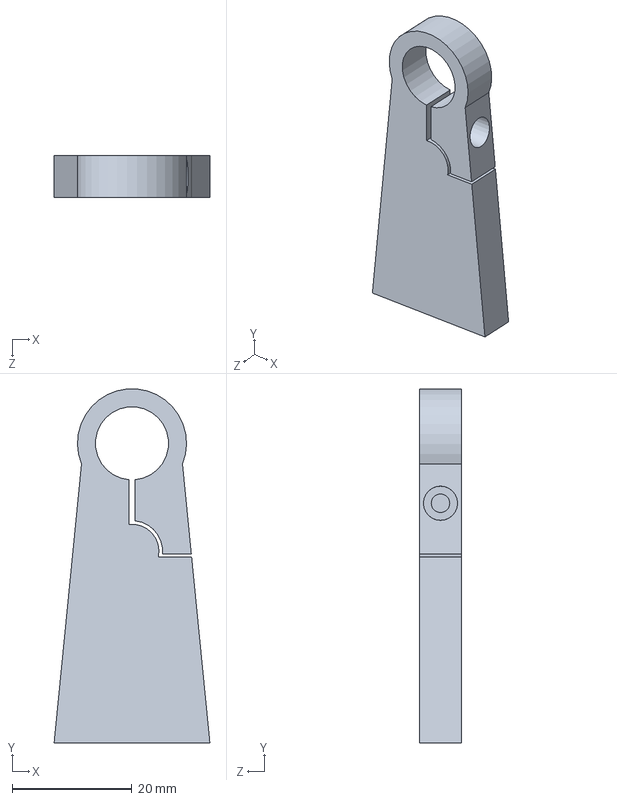
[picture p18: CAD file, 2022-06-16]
Design/MechanicalDesign/RailMounting/TopRail/PrtTopGimbalNutInsert.SLDPRT
26.0 x 59.1 x 7.00 mm

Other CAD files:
Design/MechanicalDesign/RotorBoomMounts/LGLegMountTopV3.1.SLDPRT
Design/MechanicalDesign/RotorBoomMounts/NutInsert/LGLegMountTopV3.2NutInsert.SLDPRT
Design/MechanicalDesign/SensorMounts/C-TypeSocketMounts/SimpleCase/SimpleCaseBatPMount.SLDPRT
Design/MechanicalDesign/SensorMounts/NiTubeMounting/NiTubeMount.SLDPRT
Design/MechanicalDesign/BatteryPlate/BatPlateBtFlyNut.DXF
Design/MechanicalDesign/BatteryPlate/BatPlateBtFlyNut.SLDPRT
Design/MechanicalDesign/BatteryPlate/WingNutExtender.STL
Design/MechanicalDesign/CenterHubs/BottomPlate/CHDoDeDoubleBotV1.2.DXF
Design/MechanicalDesign/CenterHubs/TopPlate/CHObDoubleTopV1.2.DXF
Design/MechanicalDesign/GPSMounts/Ai1HEREGpsMount.STL
Design/MechanicalDesign/GPSMounts/Ai1HEREGpsMountLong.STL
Design/MechanicalDesign/GPSMounts/GpsRailMountLong.SLDPRT
Design/MechanicalDesign/GPSMounts/HEREGpsBSimple.SLDPRT
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

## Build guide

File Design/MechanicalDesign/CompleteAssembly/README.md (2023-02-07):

# Complete Assembly Files
This folder contains the complete assembly zip files for both the Hex and Quad configurations.
Each folder contains the complete set of required components to create the entire frame assembly for either the Hex or Quad.

<a href="https://github.com/landrs-toolkit/LANDRs-Science-Drone/blob/main/docs/Images/Aesthetic/HexaQuadTracing.jpg">
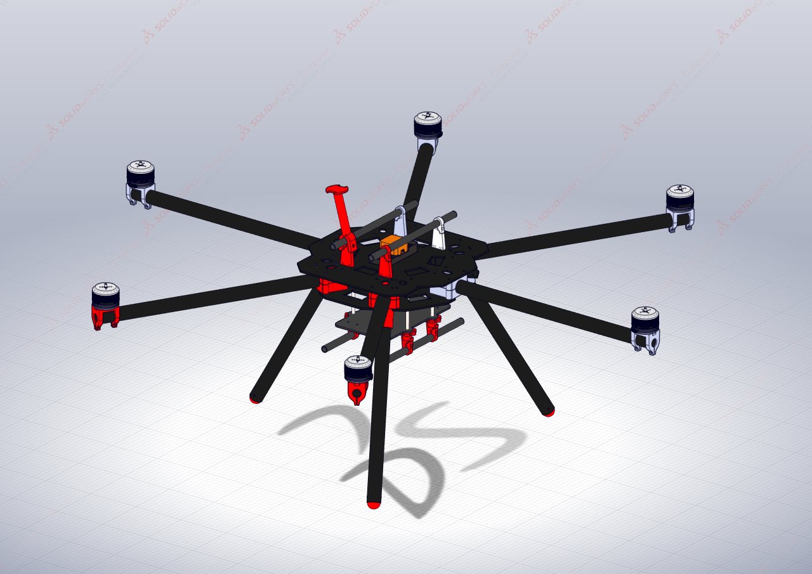
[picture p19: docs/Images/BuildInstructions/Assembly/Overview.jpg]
AssemblyRender
         
 </a>

These files can be used for illustrative purposes, to guide the user through assembly or acquire all the required components in a single folder download.

## Viewing the Assemblies:
- Solidworks 2020 or later is required to open the assemblies.
- **Hex File:** FrameHEXAsmV1.asm
- **Quad File:** FrameQUADAsmV1.asm

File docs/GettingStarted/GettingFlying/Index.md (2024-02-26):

---
layout: default
title: Getting Flying
nav_order: 2
has_children: false
description: "A guide to configure the flight controller and prepare for the first flights."
permalink: /docs/GettingStarted/GettingFlying
---

# Flight Controller Configuration:
Having completed the assembly of the HexaQuad into the desired operating configuration, configuration of the flight controller can begin.
{: .fs-6 .fw-300 }

The configuration of the flight controller is not unique to the HexaQuad and thus the reader will most often be referred to the [Arducopter
Documentation](https://ardupilot.org/copter/docs/initial-setup.html).

*Outline of steps:*
1. Introduction to Arducopter's first time setup
2. Flashing the flight controller with the HexaQuad pretuned parameter files
3. Overview of Arducopter manadatory hardware configuration.

## Arducopter's First Time Setup
Arducopter is an open source autopilot software which is installed onto the flight controller to interpret the sensor signals and thus assist with flying the drone.

The basic order of operations will first require the user to download a ground control station (GCS) to connect to the flight controller and flash the required firmware. The suggested GCS is [MissionPlanner](https://ardupilot.org/planner/index.html#home), however, other GCS like QGroundControl are also suitable. The GCS will serve two main functions when working with the drone, firstly, acting as a telemetry link to control and view the state of the drone during flight, and secondly, as a portal to configure the parameters and settings of the drone as well as to review log files from flights.

It is suggested to step through the detail [Arducopter
Documentation](https://ardupilot.org/copter/docs/initial-setup.html). to flash the autopilot software onto the flight controller and complete the basic setup. These steps will not be restated here.

## Using LANDRs Tune Parameter files
When flying a drone for the first time it is likely be unstable or show erratic behaviour. The reason for this is because the autopilot has a set of control parameters which allow the controller to produce stable and responsive flight. In order to achieve this, the drone would under go a tuning process to determine a suitbale set of control parameters, known as PID values. Arducopter has a detailed section on [Tuning](https://ardupilot.org/copter/docs/common-tuning.html) you drone.

In the case of the HexaQuad, we have gone through this tuning process already and have provided two parameter files for the Hex and Quad versions, *however note, this was without any payload attached*. These parameter files will serve as a starting point for your drone as you can simply upload these parameter files to the autopilot and begin flying. It is important to note, you may want to go through the tuning process with your version of the HexaQuad to tailor the PID values to your specific build as there might be variations in weight. This is especially important if you attach relatively heavy sensors which will alter the flight characteristics of the drone. The tuning process is not too complex and can be understood by going through Arducopters [Tuning](https://ardupilot.org/copter/docs/common-tuning.html) documentation. The autotune is especially helpful and was the process used to achieve HexaQuad's tune parameters.

[HexaQuad Parameter Files](https://github.com/landrs-toolkit/LANDRs-Science-Drone/tree/main/GettingStarted/GettingFlying){: .btn}

*Note: the parameter file contains all the settings of the drone ranging from frame type to battery capacity and voltage. Its imperative you review these values and that they match **your** setup.*

## Hardware Calibration
Prior to flying and as part of the configuration process there are a number of systems that need to be calibrated. Arducopter outlines these [Mandatory Calibration](https://ardupilot.org/copter/docs/configuring-hardware.html) steps in their documentation and it is critical to become familiar with these process to ensure correct operation of the drone.

GCS generally have tools built in that assist with the mandatory calibration of the hardware systems with step by step instructions. However, some processes like the ESC calibration is more rudimentary and is somewhat dependent on the model of ESC. Thus it is suggested to meticulously step through the mandatory hardware calibration documentation and complete all the steps as they are flight critical.

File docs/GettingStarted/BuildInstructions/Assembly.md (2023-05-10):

---
layout: default
title: "6. Assembling the HexaQuad"
parent: Build Instructions
nav_order: 7
---

# Assembly of the HexaQuad
{: .no_toc }
This section will illustrate how to assemble the HexaQuad using the Hex configuration as an example, any differences with the Quad configuration will be highlighted when necessary.
These instructions are going to use all the previous assemblies constructed in the previous steps

## Table of Content:
{: .no_toc .text-delta }

1. TOC
{:toc}

## Requirements: 

### Hex Parts:

| Component | Quantity | Description |
|:---|:---|:---|
|[Rotorboom](../../GettingStarted/BuildInstructions/Rotorbooms.md)|6| Assembled rotorbooms|
|[Landing Gear](../../GettingStarted/BuildInstructions/LandingGear.md)|3|Assembled carbon fiber rod landing gear|
|[Battery & Bottom Plate](../../GettingStarted/BuildInstructions/BatPlate.md)|1|Assembled bottom and battery plates|
|[Top Plate](../../GettingStarted/BuildInstructions/TopPlate.md)|1|Top plate with the flight controller and rails connected|
|M4x50mm Bolts|12|Hex socket bolts to secure plates|
|M4 Standard Nuts|12|Standard nuts to secure plates|
|M4 Standard Washers|24|Standard washers to secure plates|

### Quad Parts:

| Component | Quantity | Description |
|:---|:---|:---|
|[Rotorboom](../../GettingStarted/BuildInstructions/Rotorbooms.md)|4| Assembled rotorbooms|
|[Landing Gear](../../GettingStarted/BuildInstructions/LandingGear.md)|4|Assembled carbon fiber rod landing gear|
|[Battery & Bottom Plate](../../GettingStarted/BuildInstructions/BatPlate.md)|1|Assembled bottom and battery plates|
|[Top Plate](../../GettingStarted/BuildInstructions/TopPlate.md)|1|Top plate with the flight controller and rails connected|
|M4x50mm Bolts|8|Hex socket bolts to secure plates|
|M4 Standard Nuts|8|Standard nuts to secure plates|
|M4 Standard Washers|16|Standard washers to secure plates|

### Tools:
- A hand drill is useful and saves time and energy
- Socket set to tighten the nuts

## Assembling the HexaQuad
These instructions make use of the Hex configuration as an example however the Quad assembly is very similar and an variations will be identified.

CFTube

Before assembly begins, make sure to identify the correct mounting holes for the desired configuration.
The landing gear, rotorboom and battery plate mounting holes for the Hex and Quad configurations are highlighted below:

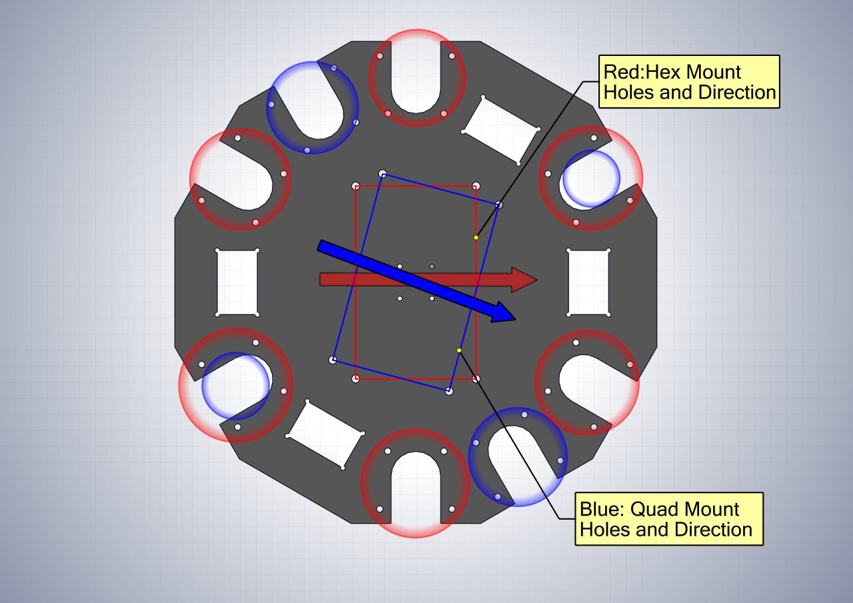
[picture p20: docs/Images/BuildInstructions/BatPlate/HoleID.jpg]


The circles in the figure above indicate rotorboom and landing gear mounting locations.
The **blue circles** are for the **Quad** and the **red circles** are for the **Hex**.
Guidance on choosing the best Hex landing gear locations will be highlighted below. The Quad configuration requires landing gear at all the rotorboom locations.

### Step 1, *Mounting the landing gear to the bottom plate*

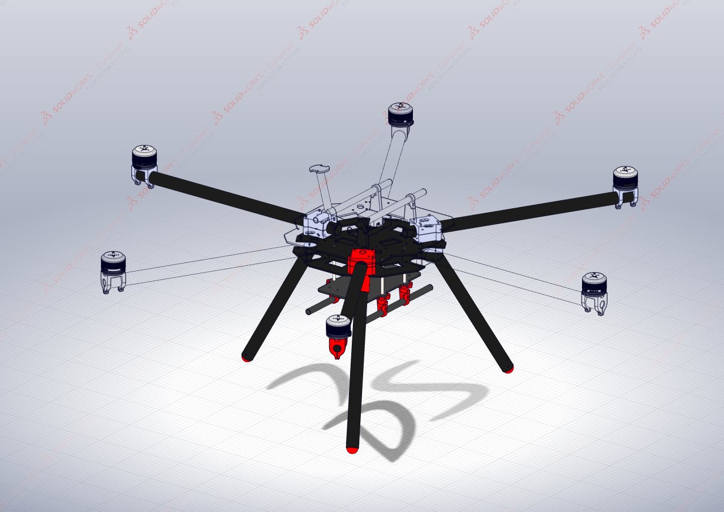
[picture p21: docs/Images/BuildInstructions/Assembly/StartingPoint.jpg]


Align the landing gear mounts into their mounting locations as identified in the mounting hole image above.
To secure the landing gear and rotorbooms, a minimum of two **M4x50mm** hex bolts and washers are required per mount, it is further suggested to use washers on the top and bottom carbon fiber plates to prevent damage.

Do not fasten the bolts tightly as the rotorbooms still need to be inserted.

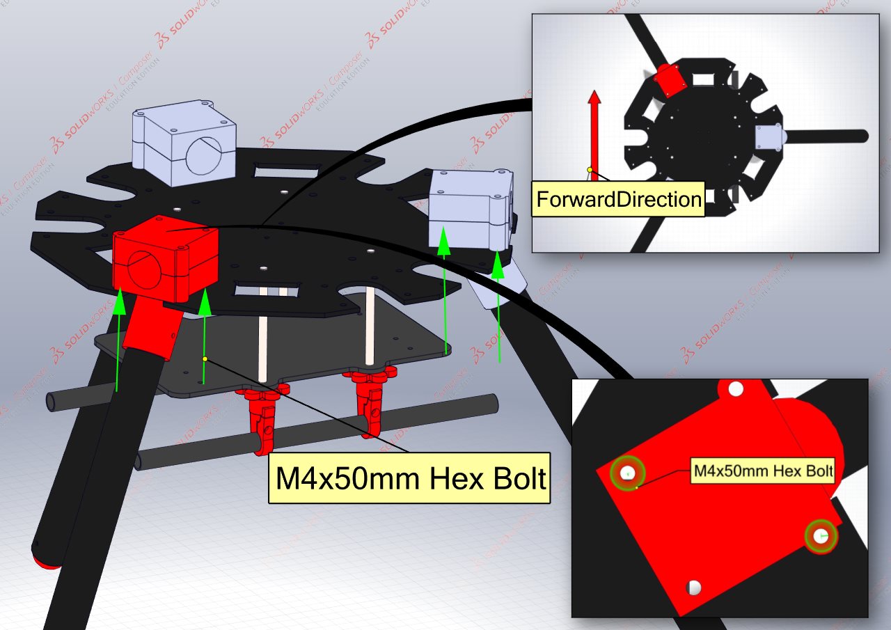
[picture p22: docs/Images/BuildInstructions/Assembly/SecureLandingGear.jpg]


### Step 2, *Adding the Rotorbooms*
When inserting the rotorbooms, ensure the inner ends of the carbon fiber tubes are 20mm away from the back of the 3D printed mount, as seen in the Figure below:

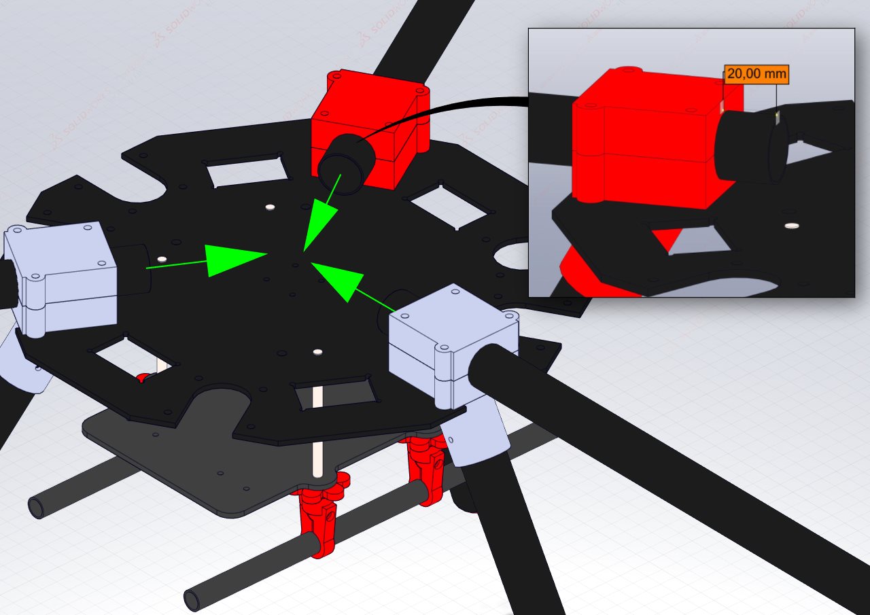
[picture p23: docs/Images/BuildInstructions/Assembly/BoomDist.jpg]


*A useful tip is to mark this point on the carbon fiber tubes to make replacement quick and avoid measurement each time.*

Tighten the M4 bolts by hand.
The final result of placing all the rotorbooms should look as follows:

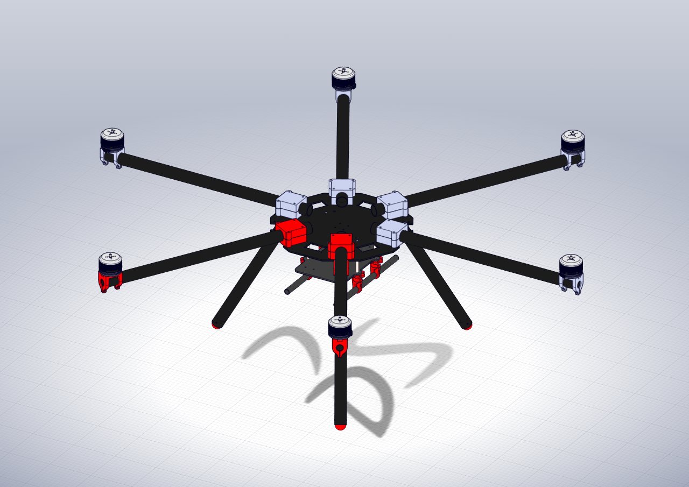
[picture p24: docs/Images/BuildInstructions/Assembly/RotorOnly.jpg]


### Step 3, *Connecting all the power distribution wires*
With all the rotorbooms inserted and semi-secured, connect the motor power distribution cables which were created in the PDB section of the guide.

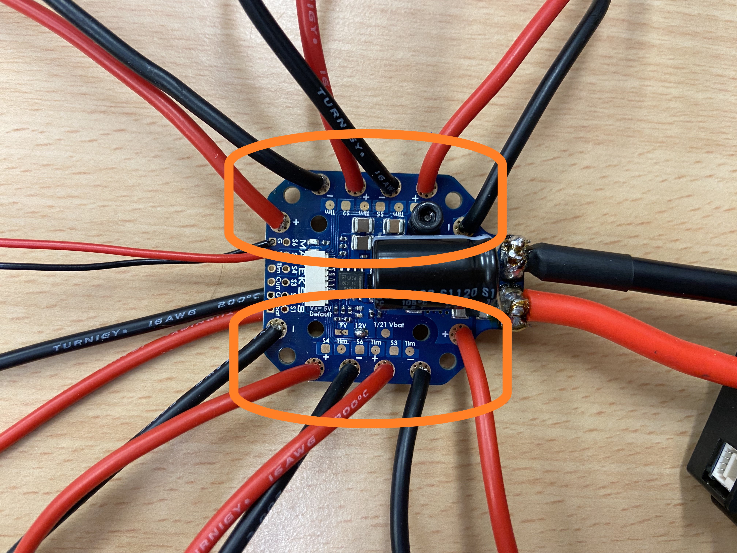
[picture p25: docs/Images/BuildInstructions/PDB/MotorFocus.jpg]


All the wires are the same and do not need to connect to a specific motor, however, it is encouraged to perform this operation with cable management in mind.

All other relevant wires for the directional LEDs and power distribution for the peripheries should be connected now too.

### Step 4, *Connect the Top Plate*
With the PDB secured and all the relevant wires connected the top plate can be put in place.
Once the plate is in place, the **M4** bolts can be secured with the relevant nuts and washers.

With the top plate in place the drone constrution is complete and should look as follows:

CFTube

[Previous Section](../../GettingStarted/BuildInstructions/PDB.md){: .btn} [Next Section](../../GettingStarted/BuildInstructions/Assembly.md){: .btn .float-right}

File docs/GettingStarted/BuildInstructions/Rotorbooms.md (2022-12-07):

---
layout: default
title: "2. Rotorbooms"
parent: Build Instructions
nav_order: 3
---

# Rotorbooms
{: .no_toc }
The rotorbooms are how the motors are connected to the central hub. This assembly incorporates the Motors, their mounts, the rotorbooms and the ESCs.

## Table of Content:
{: .no_toc .text-delta }

1. TOC
{:toc}

## Requirements: 

### Parts:

| Component | Hex Quantity | Quad Quantity | Description |
|:---|:---|:---|:---|
| [Motor Mount](https://github.com/landrs-toolkit/LANDRs-Science-Drone/blob/main/Design/MechanicalDesign/MotorMounts) | 6 | 4 | Printed motor mount |
| Carbon Rotorboom | 6| 4 | 25x23x500mm length of carbon tube |
| [T-Motor MN5008](https://store.tmotor.com/goods.php?id=999) | 6 | 4 | 6S 340KV electric motor |
| [Xrotor Pro 40A ESC](https://www.hobbywing.com/goods.php?id=400&filter_attr=15045) | 6 | 4 | 40A Electric speed controllers |
| M3 30mm bolt | 36 | 24 | M3 socket head 30mm bolt|
| M3 standard Nut | 12| 8 | M3 standard nut for 3D prints|

## Assembling the Rotorbooms:

The following illustrations will assist with assembling the rotorbooms of the HexaQuad. Repeat the following steps 6 times for Hex or 4 times in the case of the Quad configuration.

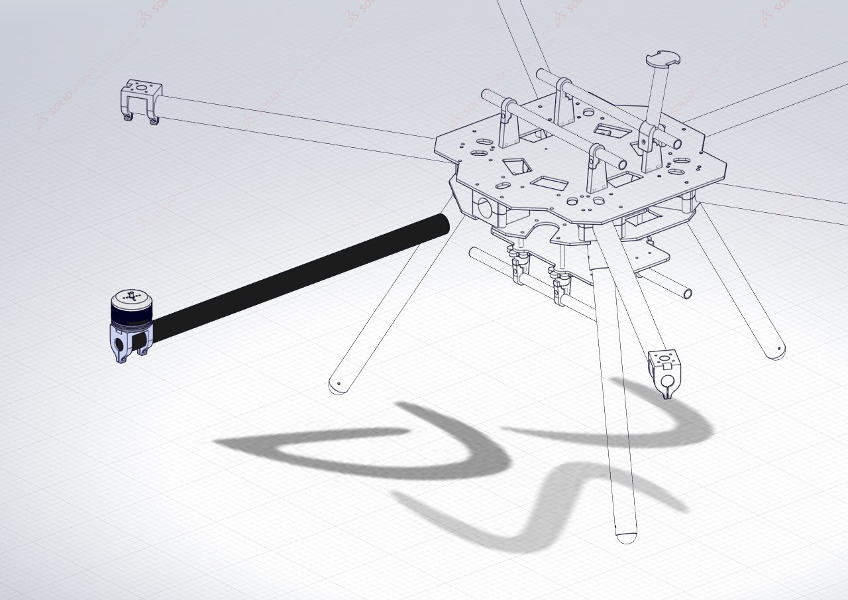
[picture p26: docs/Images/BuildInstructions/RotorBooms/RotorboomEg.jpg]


### Step 1: *Attaching the motors to the mounts*

Fit the motor onto the printed mount, aligning the mounting holes. Use **4 x M3x10mm** hex socket bolts to secure the motor to the mount. 

When aligning the motor on the mount, ensure the motor power cables are on the same side as the "Wire guide notch" of the motor mount.

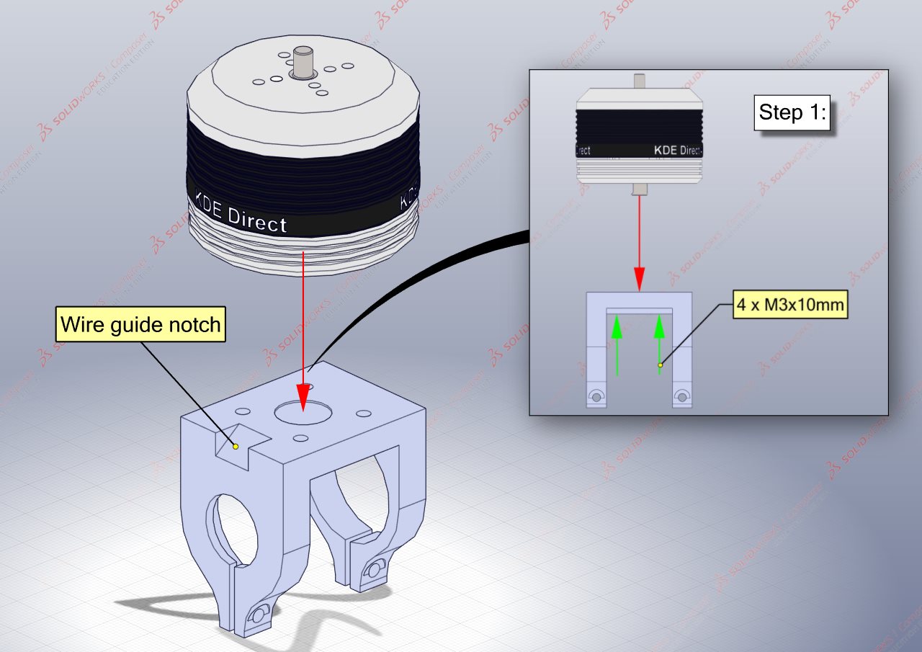
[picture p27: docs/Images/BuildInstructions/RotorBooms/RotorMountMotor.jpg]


### Step 2: *Fitting the ESC inside the carbon rotorboom*

With the motor mounted, now guide the motor power wires through the opening as shown below.

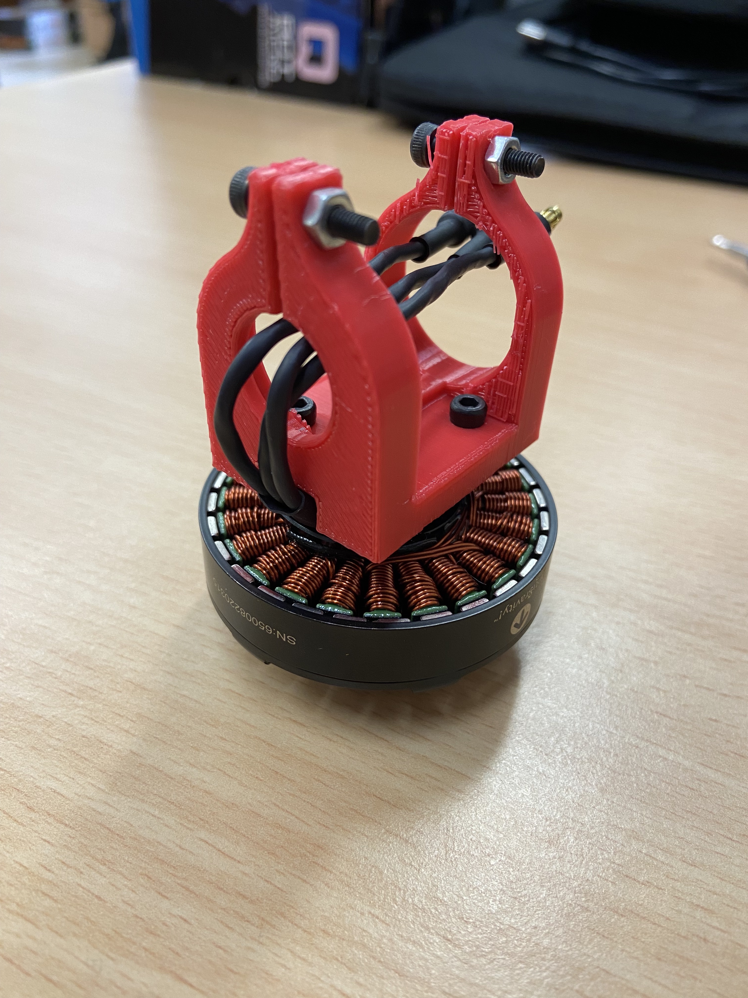
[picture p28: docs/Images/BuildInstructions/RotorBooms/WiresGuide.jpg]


There after, the ESC can be connected to the wires via the bullet connectors. Be sure to confirm the wire connection order for the two rotation directions.

Once satisfied the connection direction is correct, the ESC connected to the motor can now be slipped into the carbon fiber rotorboom.

**NOTE: It is recommended to put hot glue around the bullet connections to ensure they do not come loose!**

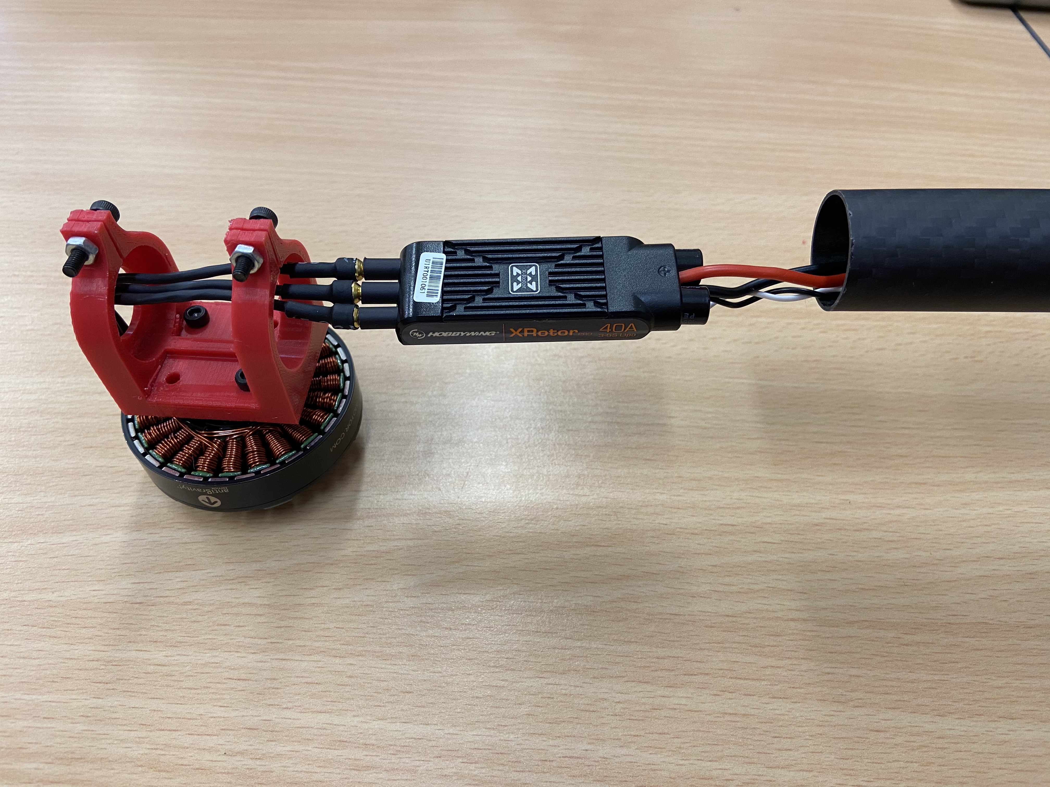
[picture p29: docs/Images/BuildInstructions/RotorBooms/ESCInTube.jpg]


Push the ESC into the tube. Gently pull on the ESC power wires whilst sliding the tube in the opposite direction until the ESC is inside the rotorboom and the end of the rotorboom is flush with the stopper end of the motor mount.

With either a pencil or marker and tape, label the motor direction on the rotorboom for ease of identification.

### Step 3: *Securing the rotorboom to the motor mount*

Finally, using **2 x M3x10mm** hex socket bolts and **2 x M3** standard nuts, secure the rotorboom to the motor mount.

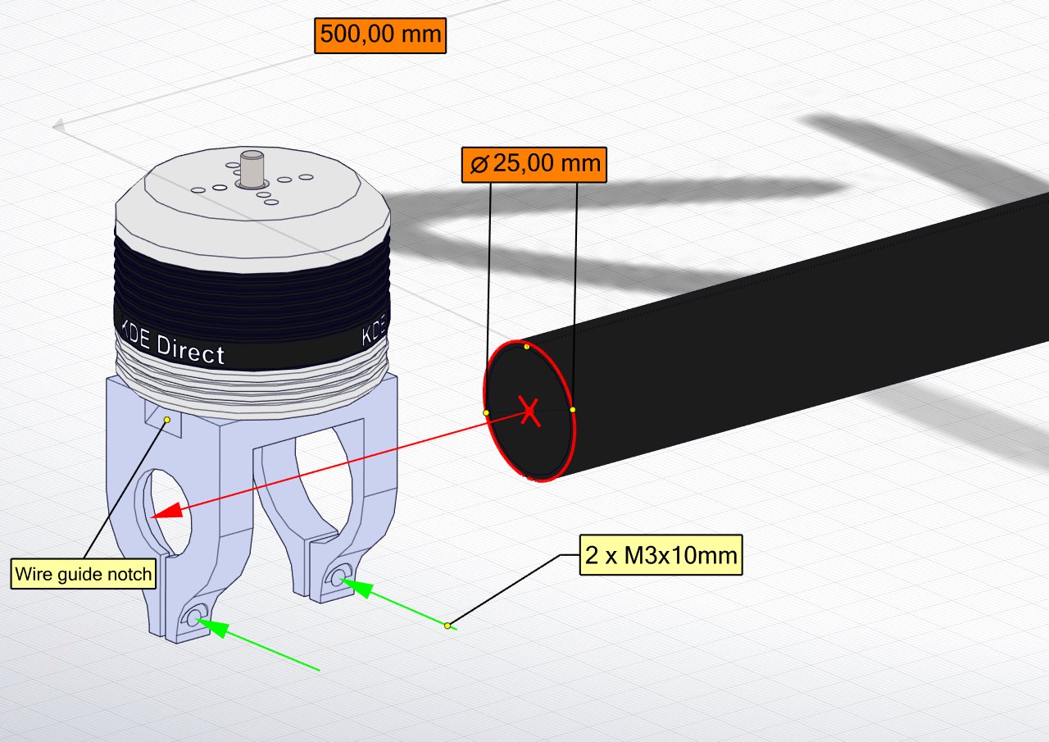
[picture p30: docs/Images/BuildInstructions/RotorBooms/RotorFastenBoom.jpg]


## Labeling the Rotorbooms:
It is recommend to label the rotorbooms by motor number, this makes assembly easier as the flight controller expects certain motors to be in certain locations as shown below:

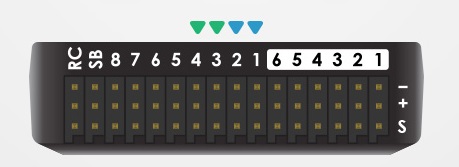
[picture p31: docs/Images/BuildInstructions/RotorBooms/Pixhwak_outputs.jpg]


|Hexacopter Motors|Quadcopter Motors|
|:----|:----|
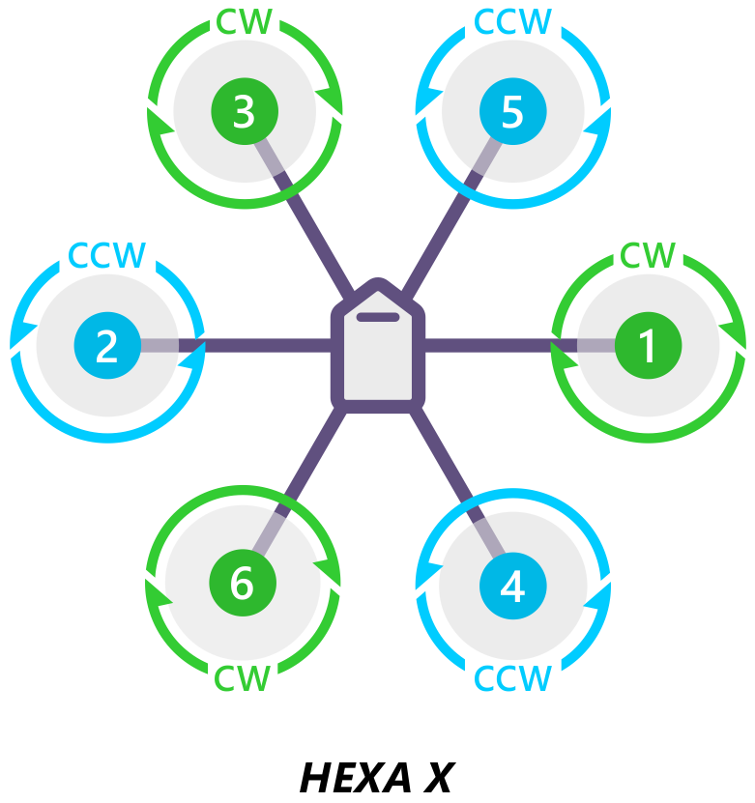
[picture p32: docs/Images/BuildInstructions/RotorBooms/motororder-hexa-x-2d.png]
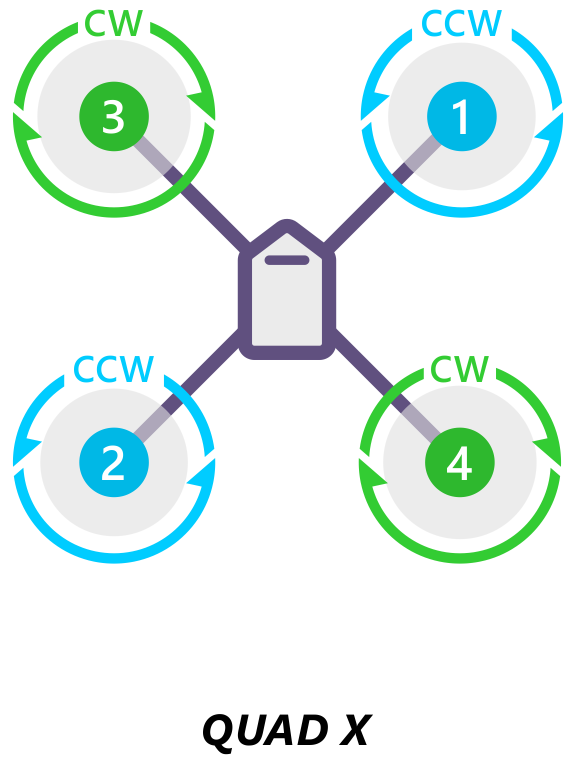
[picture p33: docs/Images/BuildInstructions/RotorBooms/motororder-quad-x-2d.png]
|||

With a marker, write the number of the motor on the ESC signal lead as follows

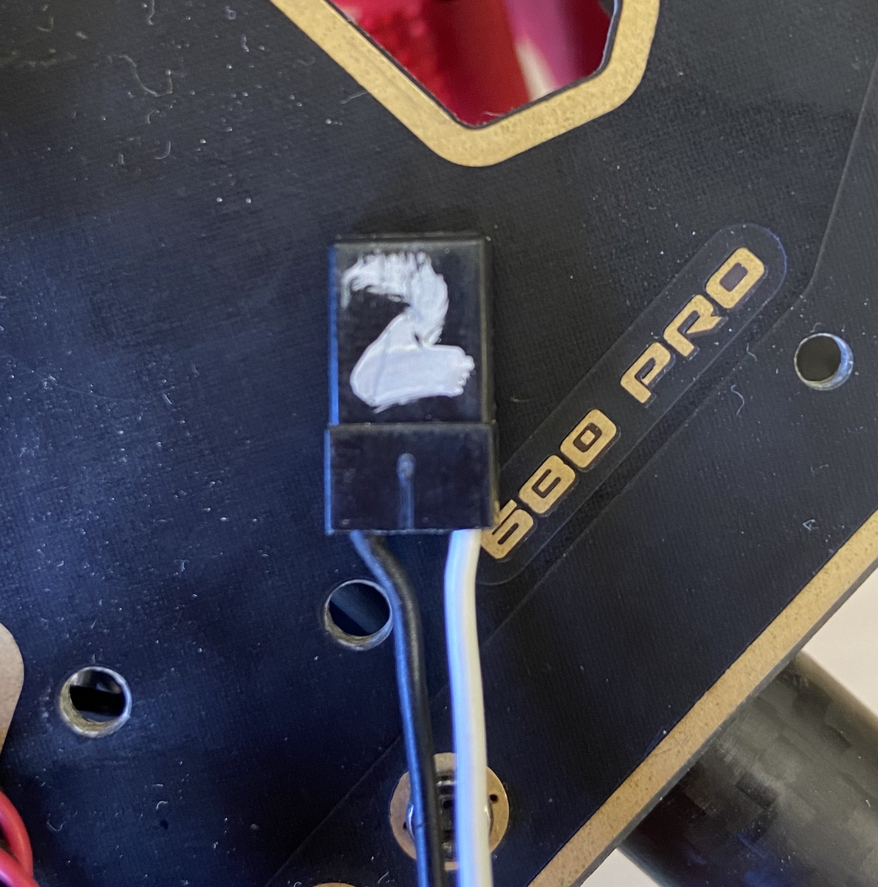
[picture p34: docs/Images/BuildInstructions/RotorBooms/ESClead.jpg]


## Clockwise or Counter Clockwise ESCs:

There are two directions the motors can turn, clockwise (CW) and counter clockwise (CCW). This requires slightly different connections between the motor and ESC. In both configurations, half of the motors will be CW and the other half will be CCW.

|Configuration| CW Motors|CCW Motors|
|:--|:--|:--|
|Hex|3|3|
|Quad|2|2|

**To ensure the correct result from this guide please use exactly the same orientations of motor and ESC!**

|Clockwise|Counter Clockwise|
|:----|:----|
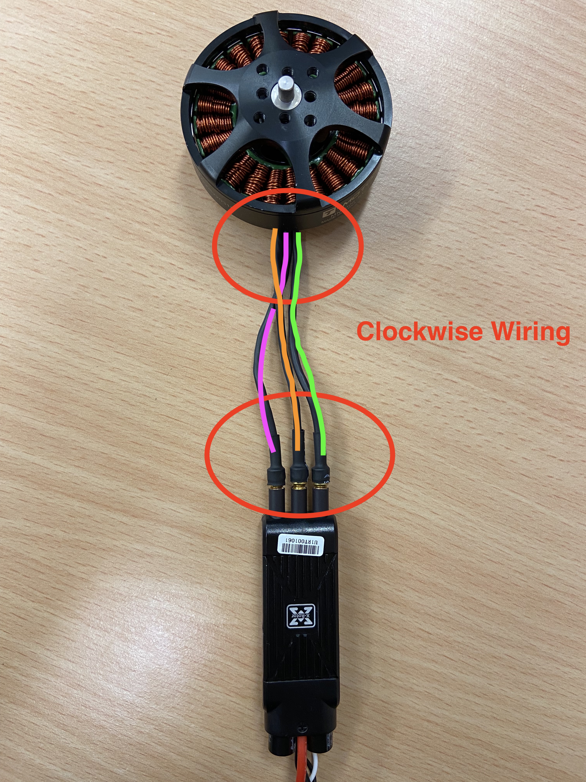
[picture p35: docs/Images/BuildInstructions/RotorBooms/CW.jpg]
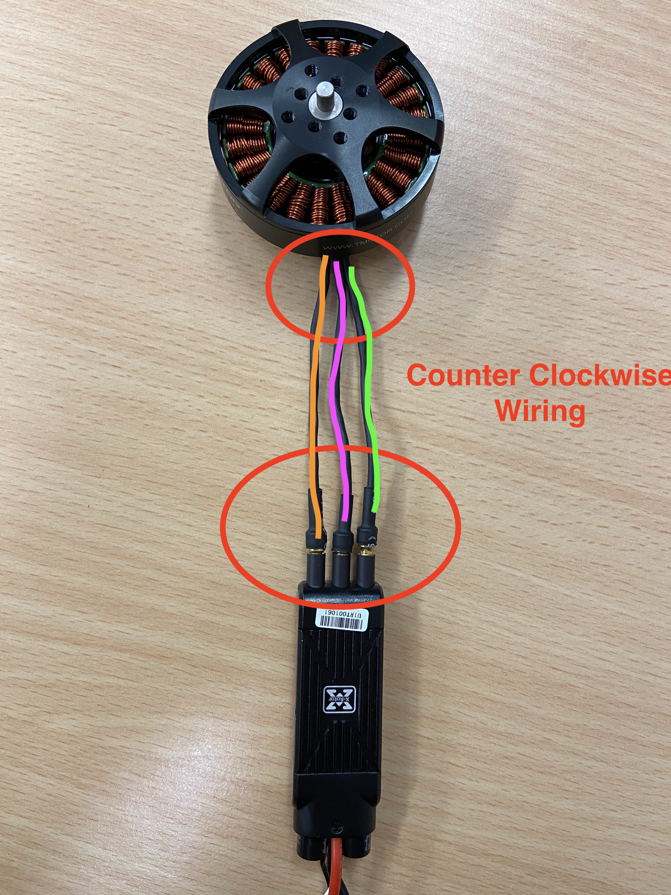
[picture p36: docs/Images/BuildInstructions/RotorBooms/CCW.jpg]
|||

[Previous Section](../../GettingStarted/BuildInstructions/LandingGear.md){: .btn} [Next Section](../../GettingStarted/BuildInstructions/TopPlate.md){: .btn .float-right}

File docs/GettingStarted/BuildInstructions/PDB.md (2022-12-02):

---
layout: default
title: "5. Power Distribution"
parent: Build Instructions
nav_order: 6
---

# Power Distribution
{: .no_toc }
This section will outline the connections of all the power carrying lines in the HexaQuad. It will detail motor connections, current sensor mounting, battery connections and periphery power connections for sensors and the autopilot. All connections will be related to the power distribution board (PDB).

*Note: These soldering instructions are only a suggestion and reference what was done in the prototype build. There are a number of other ways to create the connections outlined here, optimisation for individual cases is encouraged*

## Table of Content:
{: .no_toc .text-delta }

1. TOC
{:toc}

## Requirements: 

### Parts:

| Component | Quantity | Description |
|:---|:---|:---|
| [Matek Hex PDB](http://www.mateksys.com/?portfolio=pdb-hex) | 1 | 4-14S Power distribution board (PDB)|
| [Mauch PL-200](https://www.mauch-electronic.com/pl-xxx-sensor-boards) | 1 | Current Sensor |
| XT90-S Male | 1| Nylon wire connector with anti-spark protection |
| XT30 Male| 2 | Nylon connector|
| [PDB Mount](https://github.com/landrs-toolkit/LANDRs-Science-Drone/blob/main/Design/MechanicalDesign/PDBMount/PDBMount.STL) | 1 | 3D printed mount to secure the PDB to the bottom plate|
| Heavy Duty Velcro | 1 | 30x30mm square of velcro to secure the PDB|
| 3.5mm Female Bullets | 12 | 3.5mm female bullet connectors|
| M3 x 12mm bolt | 2 | M3 hex socket bolts to secure the PDB|
| M3 Insulator Nut | 2 | M3 plastic isolator to prevent short circuits|

## Matek Documentation:
A Matek manual for the PDB can be found [here](http://www.mateksys.com/?portfolio=pdb-hex#tab-id-1). They provide a brief instruction set for connections of either a hexacopter or a quadcopter.

## PDB Connections:
The following illustrations will assist with soldering all the required components to the PDB and its extensions. The illustrations will make use of images and diagrams for more detail.

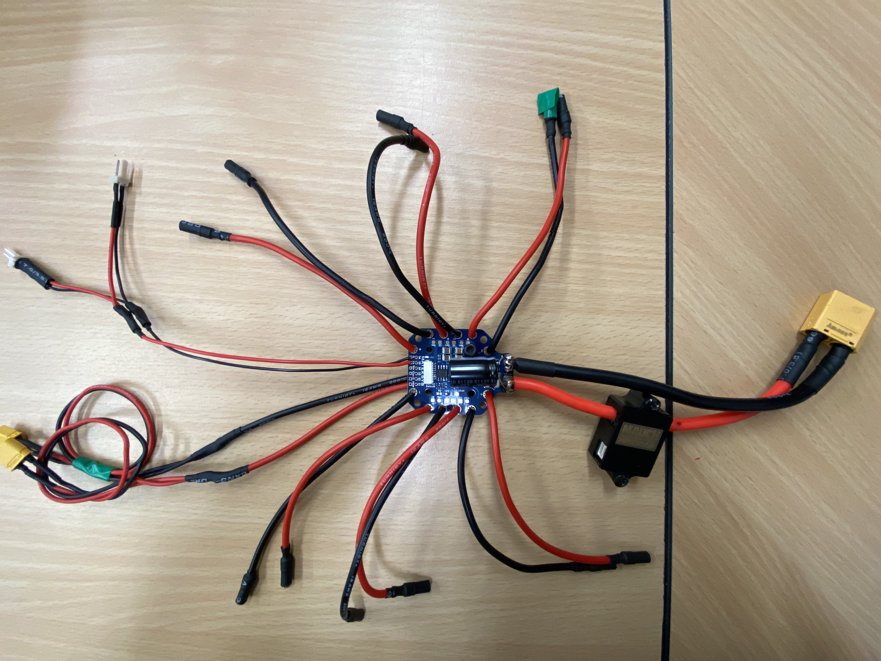
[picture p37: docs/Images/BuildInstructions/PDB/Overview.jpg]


### Step 1: *Soldering on the capacitor*
There is an input capacitor that must be soldered at the input of the PDB. The provided capacitor has a capacity of 390 micro farad and is polarised (dedicated positive and negative side).

Guide the capacitors leads through the provided holes and solder on the bottom pads

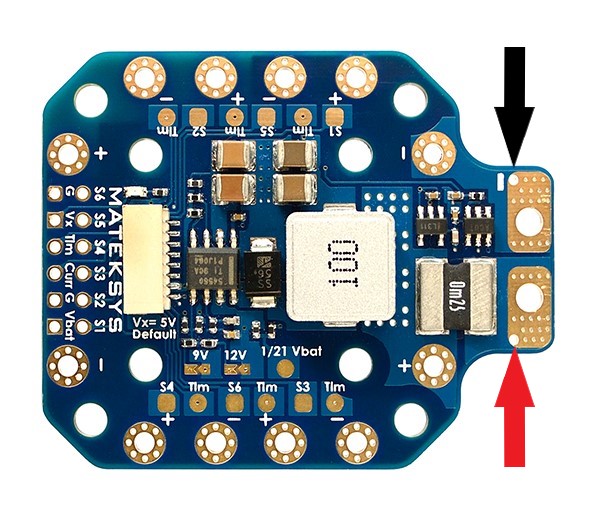
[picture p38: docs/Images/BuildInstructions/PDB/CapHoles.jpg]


The capacitor can then be bent over as follows to reduce the height of the PDB form factor.

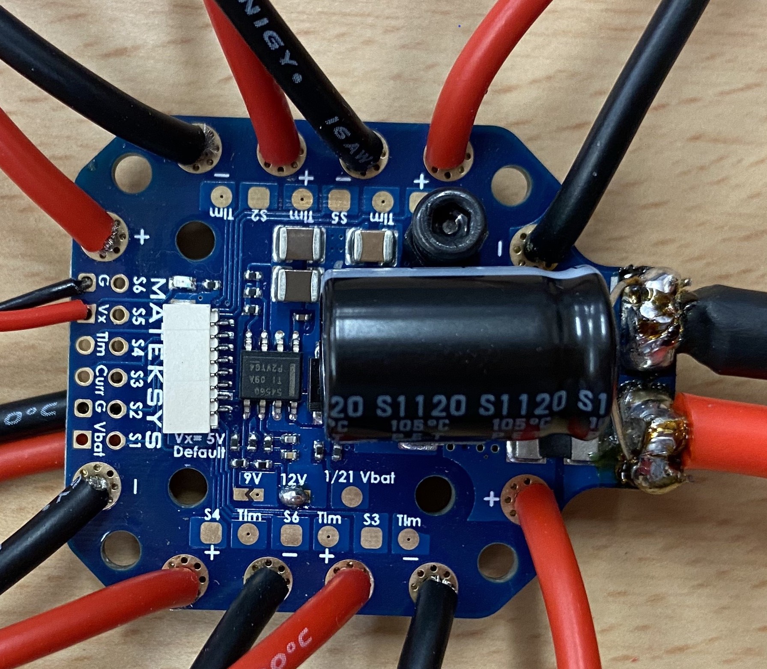
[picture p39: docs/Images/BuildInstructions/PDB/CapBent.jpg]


### Step 2: *Input wires and current sensor*
The PL-200 current sensor is connected to the input pads of the PDB. This ensures the current reading includes the actual current draw from the batteries.

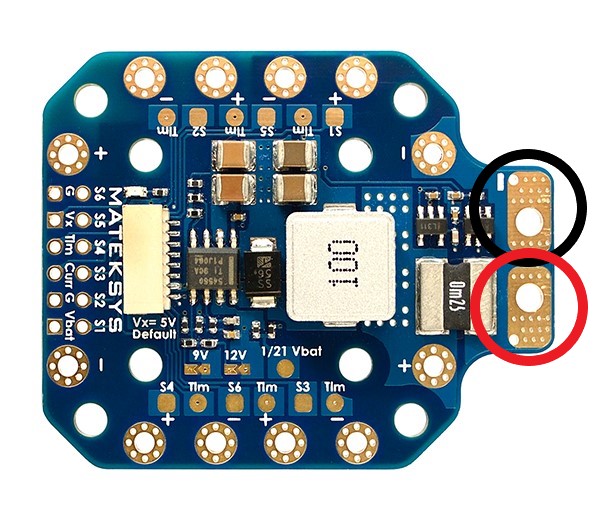
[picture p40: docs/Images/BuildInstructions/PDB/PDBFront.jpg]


The current sensor has a direction of use, the current flow direction can be identified by opening the carbon fiber protective housing.

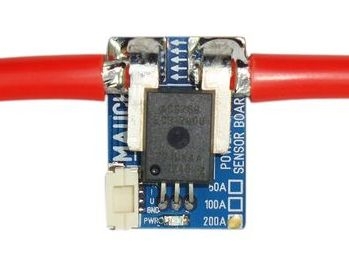
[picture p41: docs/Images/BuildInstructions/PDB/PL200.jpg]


The free end of the current sensor is connected to an **XT90** nylon connector. The entire connection should look as follows:

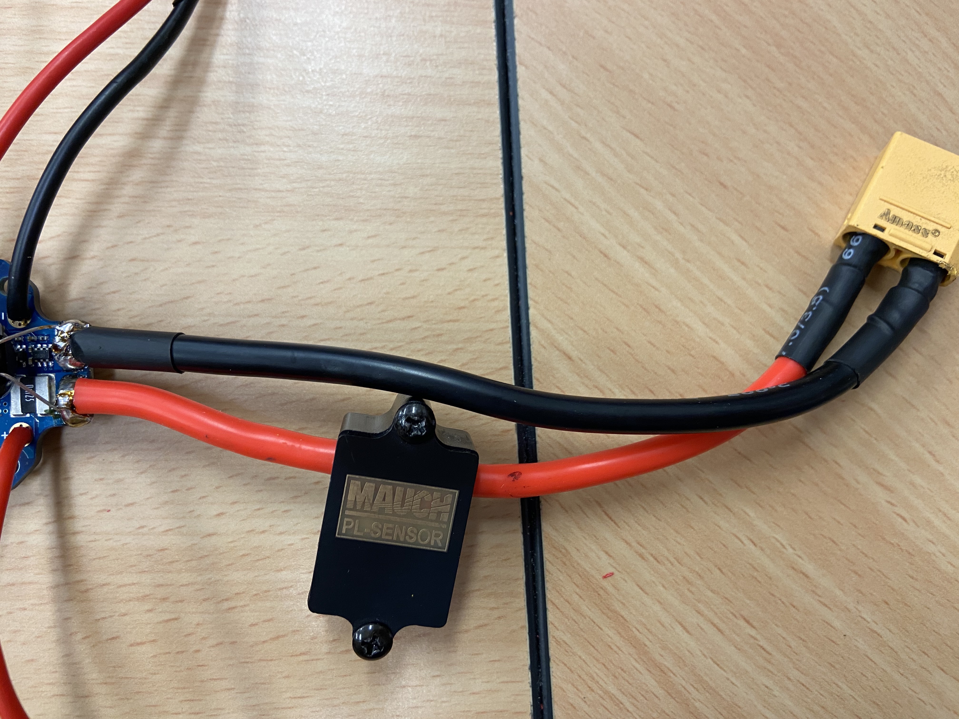
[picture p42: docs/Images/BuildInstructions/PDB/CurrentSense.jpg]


### Step 3: *Soldering on the motor wires*
The next step is to connect the motor connections. The following highlights the conductive pads that require soldering.

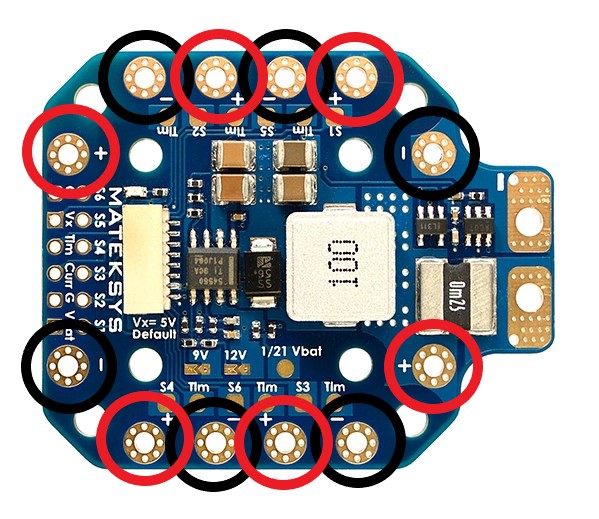
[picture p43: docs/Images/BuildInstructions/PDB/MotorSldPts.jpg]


The ends of the motor connections being soldered will need to be reduced in size to fit through the solder pad holes.

With the wire end sticking through the hole, solder the exposed wire to the bottom solder pad of the PDB. The result should look as follows:

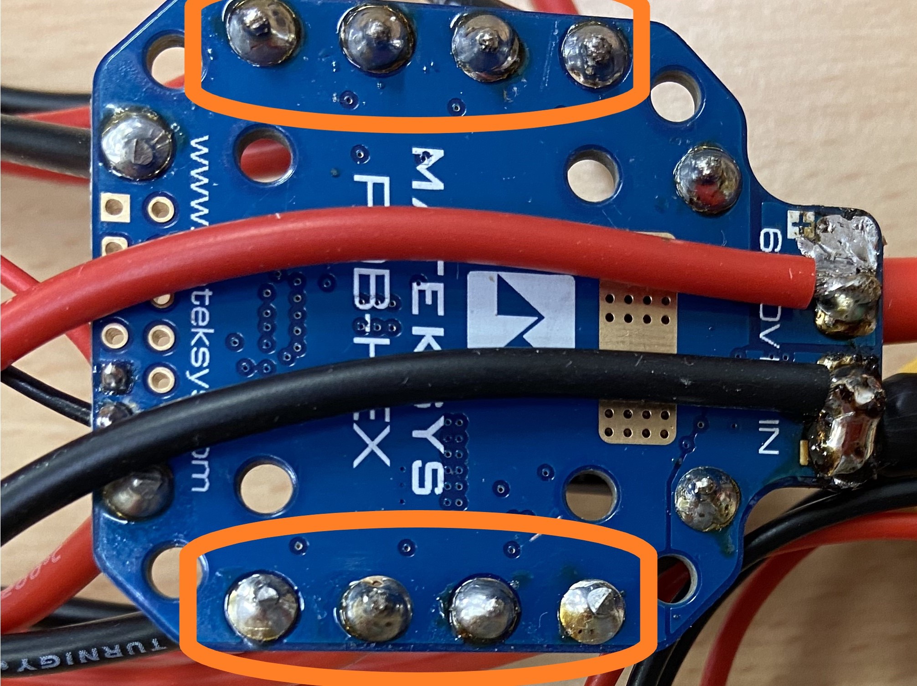
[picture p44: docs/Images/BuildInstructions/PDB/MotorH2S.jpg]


With all the motor connections solder, the end result should look as follows:

CFTube

### Step 4: *Adding periphery wires*
Some components require an input voltage at the same voltage of the battery. This step outlines adding a periphery wire to connect things like the autopilot regulator and sensor regulators.

Looking at the bottom of the PDB, the input voltage pads will be used to solder on the periphery wires. 

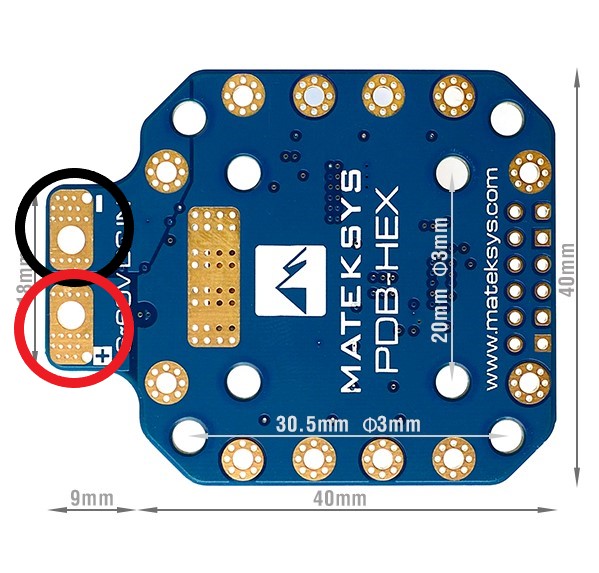
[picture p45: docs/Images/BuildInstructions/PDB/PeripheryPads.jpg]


Take the periphery wire with two **XT30** male connectors on the end and solder it to the pads shown above. The wire ends **do not** need to go through the holes here.

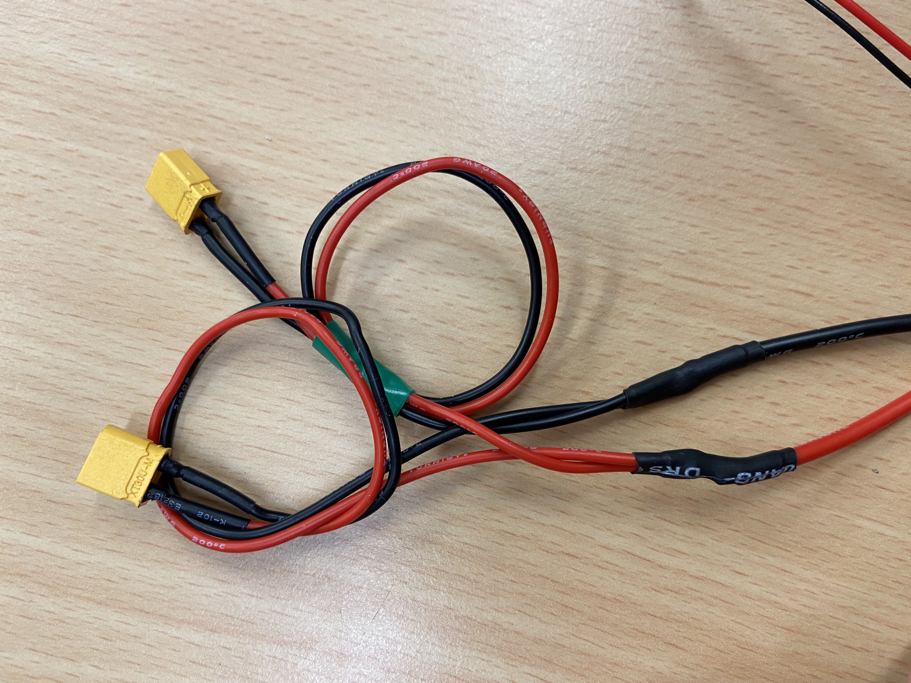
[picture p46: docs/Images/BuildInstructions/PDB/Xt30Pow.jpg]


The result should appear similar to this:

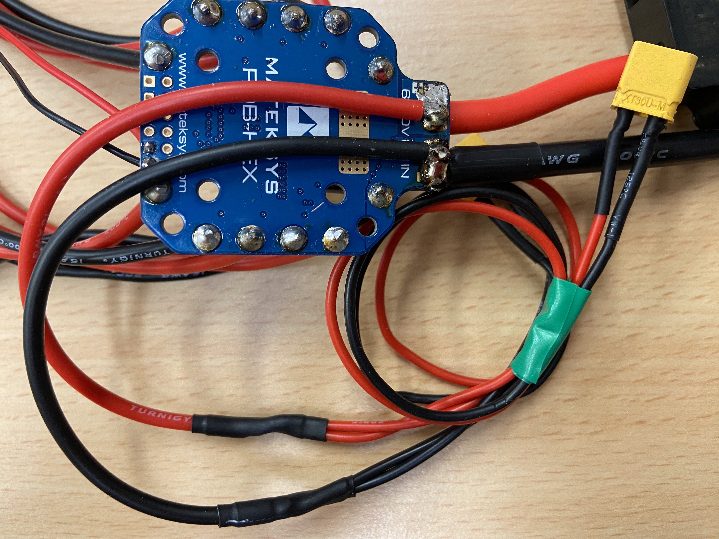
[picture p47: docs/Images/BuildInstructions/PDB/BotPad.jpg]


### Step 5 (Optional): *PDB voltage regulator*
The PDB comes with an internal voltage regulator that can output 5V, 9V or 12V at 4A.

The standard output is 5V, if one of the solder pads is connected then the output voltage will match the label.

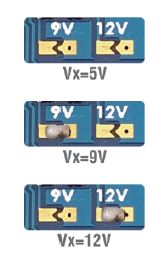
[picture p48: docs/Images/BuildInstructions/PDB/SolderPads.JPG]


The selected voltage is output from these solder pads and wires with the desired connectors can be fixed here. **Vx** is the positive terminal and **G** is the negative or ground terminal.

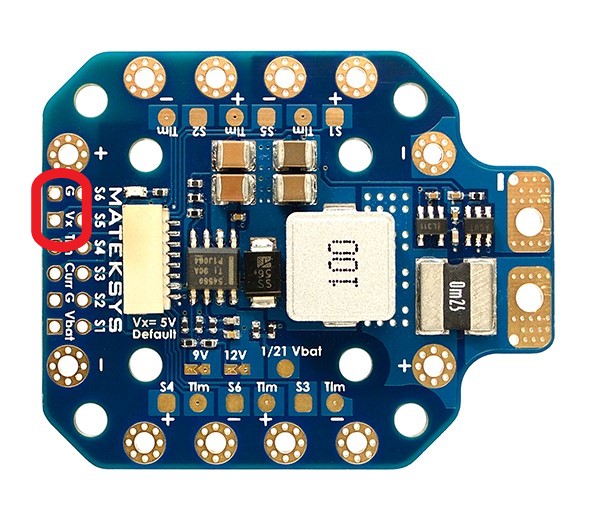
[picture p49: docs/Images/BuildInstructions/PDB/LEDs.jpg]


These solder pads can be used for flight LEDs or to power other peripheries just ensure the output voltage matches the requirements of the component in use.

## Mounting the PDB
Satisfied that the required solder on the PDB is complete, it can not be mounted to the Bottom Plate of the Central Hub.

### Step 1: *Fixing the PDB to the plate*
The PDB will be fixed to the bottom plate via two means, a 3D print with embedded nuts and velcro to secure the 3D print. The velcro is beneficial if the PDB location needs to change, i.e. for reconfiguration between Hex and Quad.

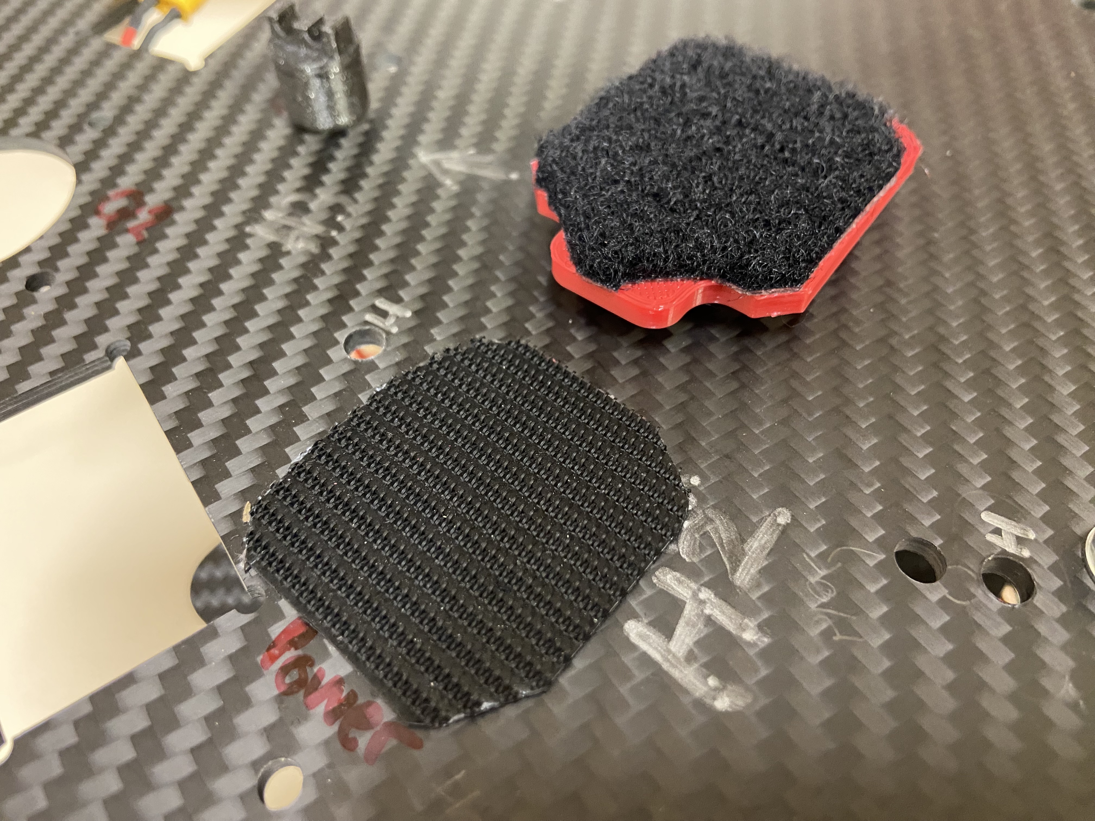
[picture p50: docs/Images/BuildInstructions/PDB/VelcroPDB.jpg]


The PDB should be placed towards the back of the Bottom plate as shown bellow. Configuration markings assist with good placement of the velcro.

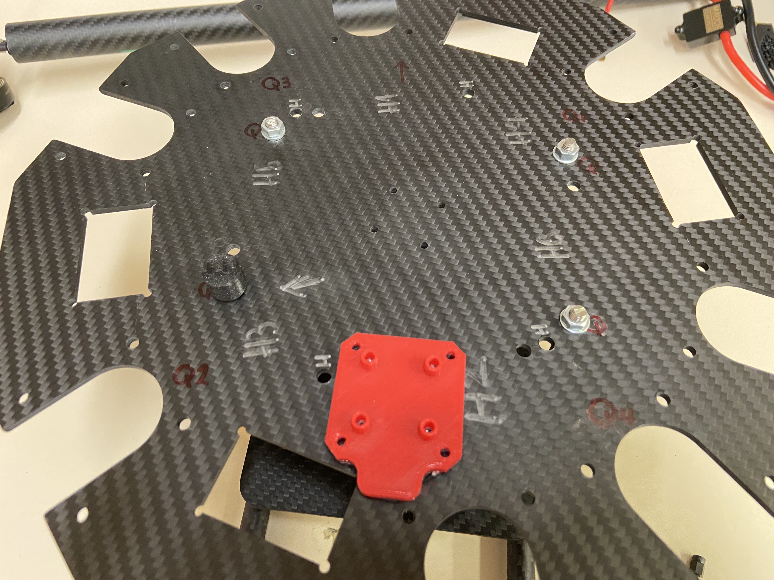
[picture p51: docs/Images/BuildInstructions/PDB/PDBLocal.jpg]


### Step 2: *Securing the PDB to the mount*
The PDB is secured to the printed mount with 2 **M3x12mm** hex socket bolts and 2 plastic insulators.

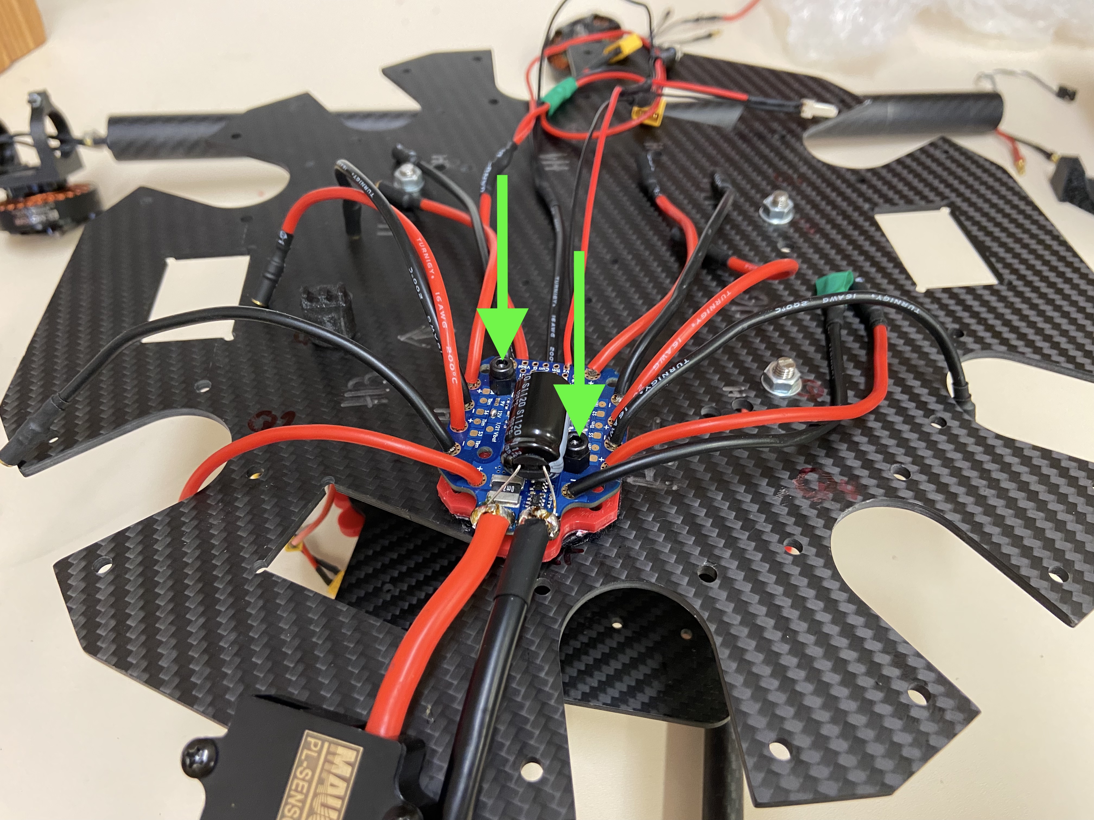
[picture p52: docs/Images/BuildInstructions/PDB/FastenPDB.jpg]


[Previous Section](../../GettingStarted/BuildInstructions/BatPlate.md){: .btn} [Next Section](../../GettingStarted/BuildInstructions/PDB.md){: .btn .float-right}

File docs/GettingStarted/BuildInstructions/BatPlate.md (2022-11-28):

---
layout: default
title: "4. Bottom and Battery Plates"
parent: Build Instructions
nav_order: 5
---

# Bottom Plates of the Central Hub
{: .no_toc }
This section focuses on assembling the bottom plates of the central hub, including the battery plate and its associated rail mounts as well as how they are secured to the bottom dodecagon plate.

## Table of Content:
{: .no_toc .text-delta }

1. TOC
{:toc}

## Requirements: 

### Parts:

| Component | Quantity | Description |
|:---|:---|:---|
| [Battery Plate](https://github.com/landrs-toolkit/LANDRs-Science-Drone/tree/main/Design/MechanicalDesign/BatteryPlate) | 1 | CNC'd carbon fiber plate |
| [Dodecagon Bottom Plate](https://github.com/landrs-toolkit/LANDRs-Science-Drone/tree/main/Design/MechanicalDesign/CenterHubs/BottomPlate) | 1 | CNC'd carbon fiber plate |
| [Wing Nut Extender](https://github.com/landrs-toolkit/LANDRs-Science-Drone/tree/main/Design/MechanicalDesign/BatteryPlate) | 4| 3D Printed wing nut extender |
| [Bottom Rail Mount](https://github.com/landrs-toolkit/LANDRs-Science-Drone/tree/main/Design/MechanicalDesign/RailMounting) | 4 | 3D Printed bottom rail mount |
| Gimbal Rails | 2 | 12x10x250mm carbon fiber tube|
| M5 x 100mm Threaded Rod | 4| M5 threaded rod to secure battery plate|
| M5 Standard Nut | 12| M5 standard nut to secure threaded rods to bottom plate|
| M5 Standard Washer | 12| M5 washer to prevent damage to carbon fiber plates|
| M3 x 8mm bolt | 4 | M3 hex socket bolts for gimbal mounts|

## Assembling the Bottom part of the Central Hub:
The following illustrations will assist with assembling the components associated with the bottom plates of the central hub. 

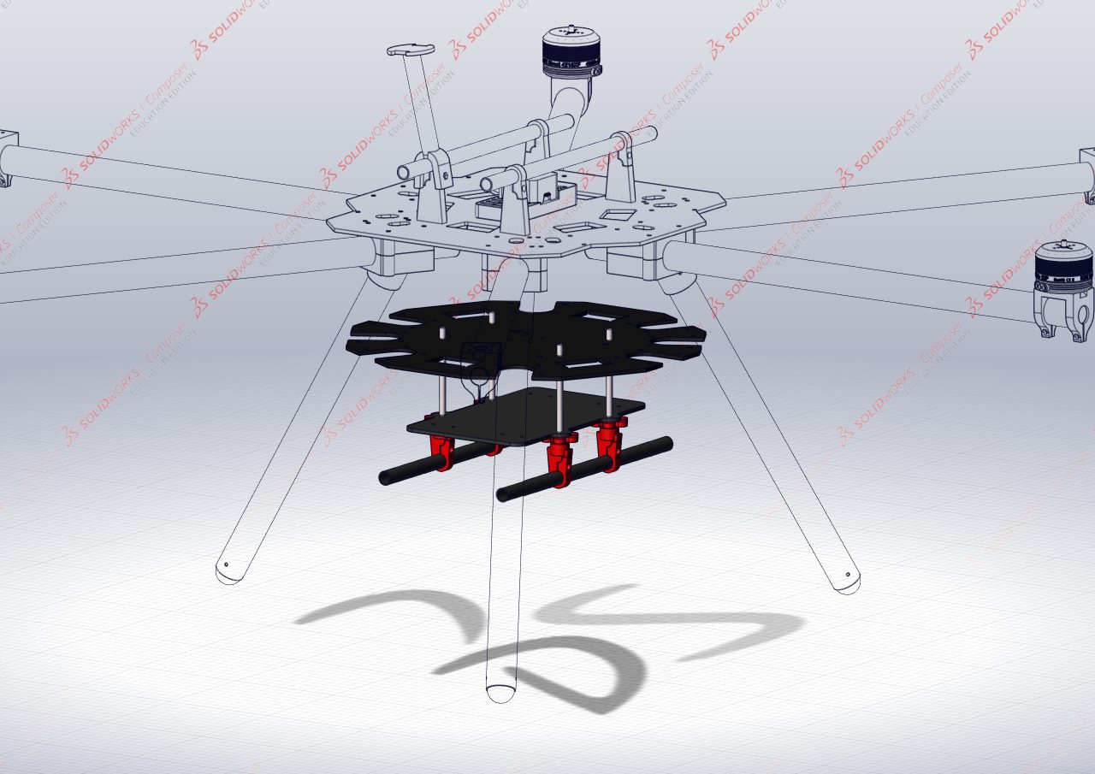
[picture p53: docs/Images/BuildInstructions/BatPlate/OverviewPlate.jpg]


### Step 1: *Bottom gimbal rail mounts*
The battery plate and bot gimbal rails are secured to the dodecagon bottom plate with **M5 Threaded Rod**. This step must be repeated 4 times.

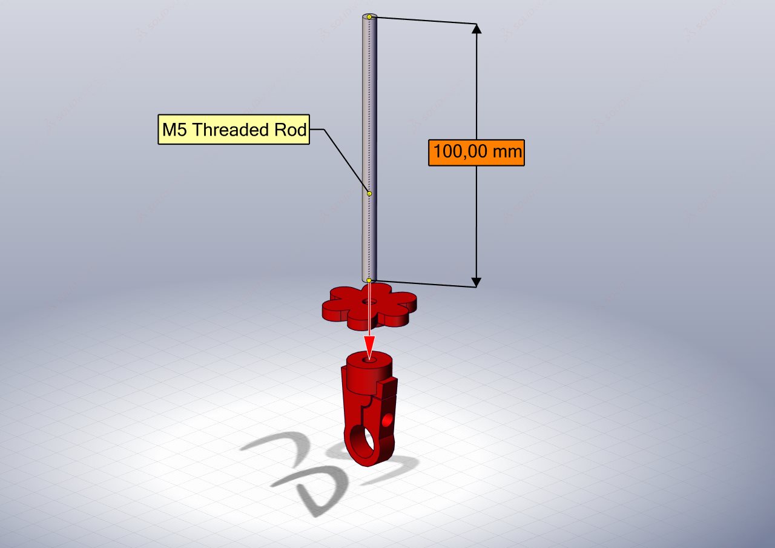
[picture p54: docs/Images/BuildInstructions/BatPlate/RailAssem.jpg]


On the bottom end of a **M5 x 100mm** threaded rod, thread on a Wing Nut Extender. Slide on a **Standard M5 Washer** on the top side of the Wing Nut.
Ensure theres enough room below the Wing Nut to secure the Rail Mount.

When threading on the Bottom Rail Mount, thread the rod in just enough to see it pass the top hole on the side of the printed mount. The thread should pass the point of the arrow below.

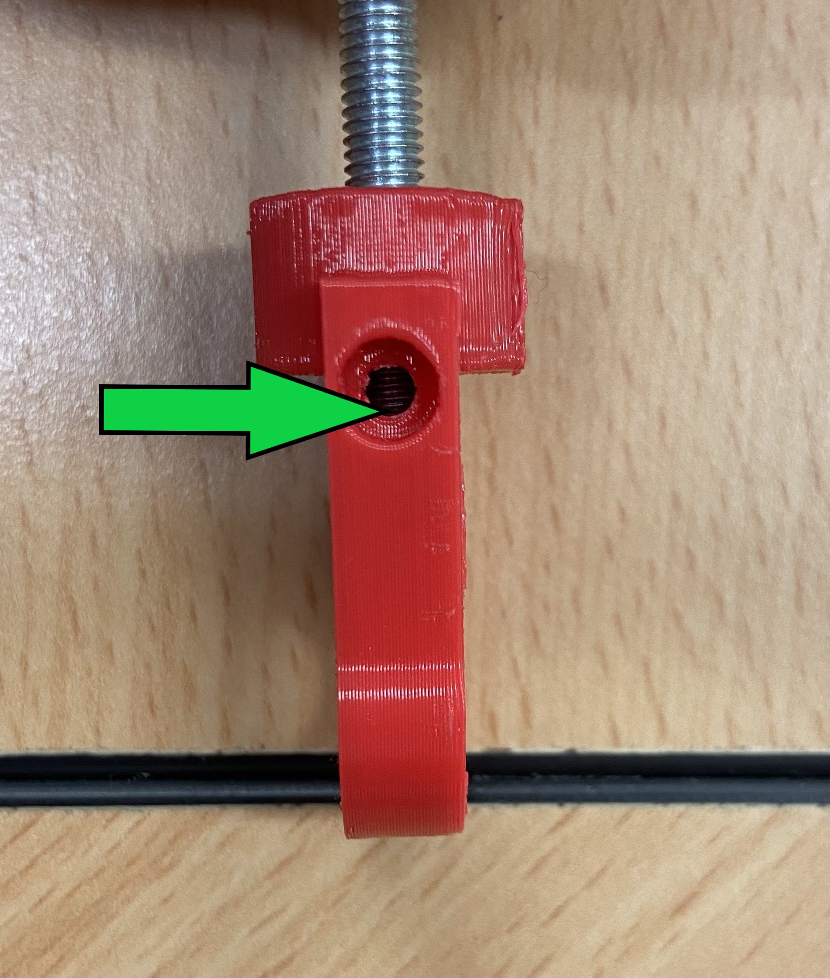
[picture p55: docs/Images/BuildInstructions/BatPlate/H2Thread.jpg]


*Note: You may thread the threaded rod as far as it will go however it will leave less thread to work with when securing the rods to the bottom plate of the central hub.*

### Step 2: *Securing the gimbal rails and battery plate*
With the 4 assembled bottom gimbal rail mounts, slide on the Battery Plate as illustrated.

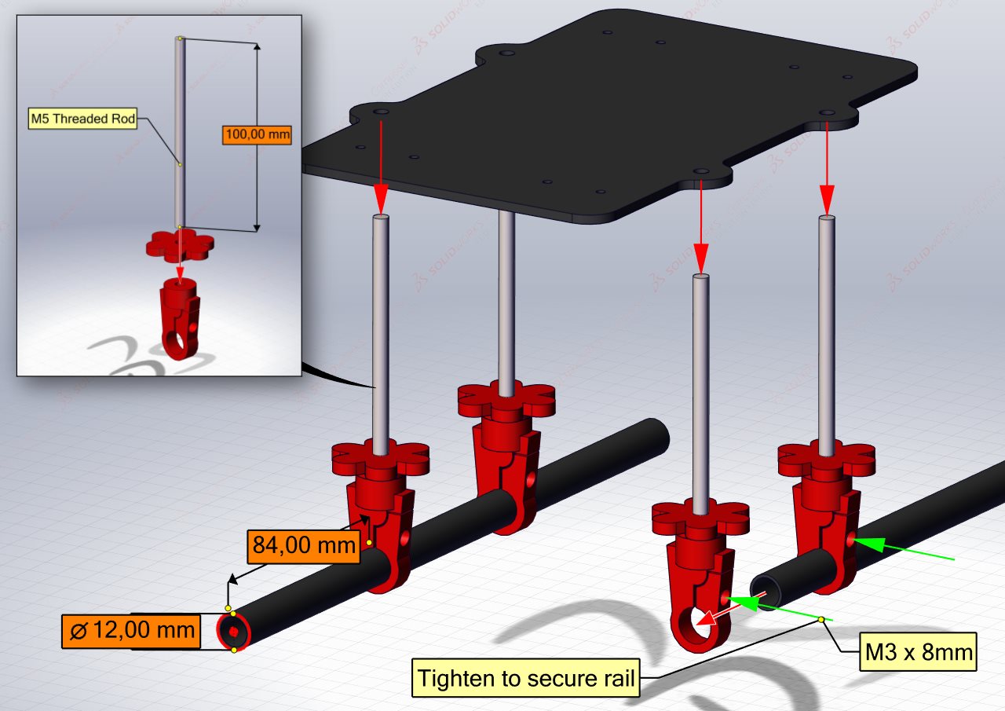
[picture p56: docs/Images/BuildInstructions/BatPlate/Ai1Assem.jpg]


The carbon fiber rails can then be secured in the rail mounts, the end of the rail should be **84mm** from the rail mount. Use **M3 x 8mm** hex socket bolts to secure the rails in place.

### Step 3: *Locking nuts to secure the battery plate to the dodecagon plate*
The Battery Mounting Plate and Rails are secured to the Bottom Dodecagon plate by means of "locked" nuts.

On each of the threaded rods, thread 2 **M5** standard nuts approximately 15mm down the rod. Then place a **M5** standard wash on top of the nuts.

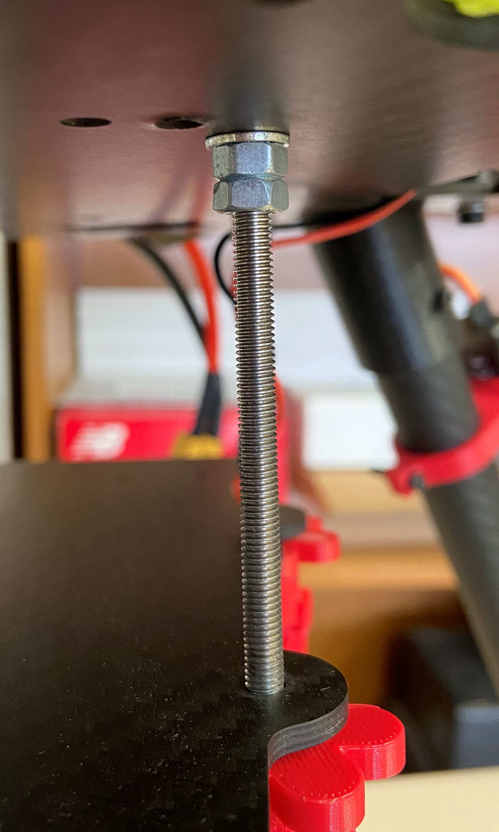
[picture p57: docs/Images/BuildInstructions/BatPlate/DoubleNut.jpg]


The nuts are "locked" by threading them towards each other until they are tight, this is easier to do with spanners.

### Step 4: *Securing the battery plate to the dodecagon plate*
There are two sets of possible mount holes on the bottom dodecagon plate. The following illustration assists with choosing the correct holes depending on the configuration you are assembling.

*Suggestion: use markers or a pencil to mark which holes for the respective configurations*

CFTube

Satisfied the correct holes have been chosen, the bottom plate mount holes can be aligned with the threaded rods and pushed through. The Bottom Plate should rest on the locked nuts from the previous step.

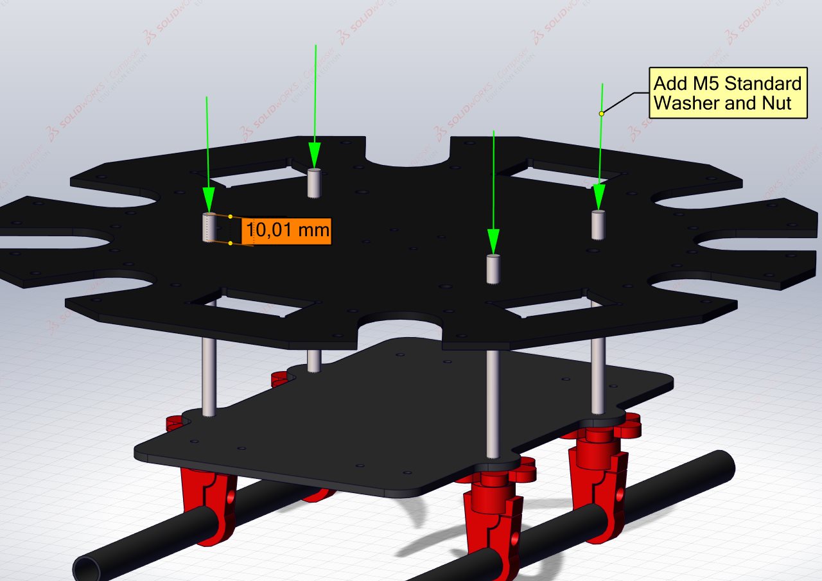
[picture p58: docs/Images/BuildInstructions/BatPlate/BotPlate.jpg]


Then add a standard **M5** washer and nut to the top of each threaded rod. Tighten the nut to secure the Bottom Dodecagon Plate to the Battery Plate assembly.

*Note: You may need to slightly adjust nut heights on each threaded rod to ensure the battery plate is as close to level as possible.*

[Previous Section](../../GettingStarted/BuildInstructions/TopPlate.md){: .btn} [Next Section](../../GettingStarted/BuildInstructions/PDB.md){: .btn .float-right}

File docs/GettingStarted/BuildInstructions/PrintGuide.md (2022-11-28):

---
layout: default
title: 3D Part Print Guide
parent: Preparation
grand_parent: Build Instructions
nav_order: 2
---

# 3D Part Print Guide
{: .no_toc}

This document outlines everything required to print the associated parts in the intended way. It will highlight the correct print orientation, if a nut insert is present, the infill percentage and layer settings.

A number of the 3D printed parts contain nut inserts for added strength. A tutorial on how to embed nuts can be found here:

[3D Print Inserts](../../GettingStarted/Tutorials/3DPrintInserts.md){: .btn}

## Table of Content:
{: .no_toc .text-delta }

1. TOC
{:toc}

# WingNut Extender:

1 x M5 Nut
{: .label .label-red}

**Orientation:**

WingNut

**Infill Percentage:** 30%

**Layer Thickness:** 0.2mm

# Landing Gear Tube Cap:

**Orientation:**

LandingGear

**Infill Percentage:** 15%

**Layer Thickness:** 0.2mm

# Top Rotor Boom Mount:

2 x M4 Nut
{: .label .label-red}

**Orientation:**

TopRotor

**Infill Percentage:** 30%

**Layer Thickness:** 0.2mm

# Bottom Rotor Boom Mount:

Requires Support Material
{: .label .label-green}

**Orientation:**

BotRotor

**Infill Percentage:** 100%

**Layer Thickness:** 0.2mm

# Motor Mount:

Requires Support Material
{: .label .label-green}

**Orientation:**

BotRotor

**Infill Percentage:** 100%

**Layer Thickness:** 0.2mm

# Top Rail Mount:

3 x M3 Nuts
{: .label .label-red}

**Orientation:**

BotRotor

**Infill Percentage:** 30%

**Layer Thickness:** 0.2mm

# Bottom Rail Mount:

2 x M3 Nuts
{: .label .label-red}

1 x M5 Nuts
{: .label .label-red}

Requires Support Material
{: .label .label-green}

**Orientation:**

BotRotor

**Infill Percentage:** 50%

**Layer Thickness:** 0.2mm

# GPS Mount:

Requires Support Material
{: .label .label-green}

**Orientation:**

BotRotor

**Infill Percentage:** 30%

**Layer Thickness:** 0.2mm

# PDB Mount:

4 x M3 Nuts
{: .label .label-red}

**Orientation:**

BotRotor

**Infill Percentage:** 30%

**Layer Thickness:** 0.2mm

# Nut Insert Tube Mount:

1 x M3 Nuts
{: .label .label-red}

**Orientation:**

BotRotor

**Infill Percentage:** 30%

**Layer Thickness:** 0.2mm

# RC Receiver Mount:

Requires Support Material
{: .label .label-green}

**Orientation:**

BotRotor

**Infill Percentage:** 30%

**Layer Thickness:** 0.2mm

# Telemetry Radio Mount:

**Orientation:**

BotRotor

**Infill Percentage:** 30%

**Layer Thickness:** 0.2mm

[Previous Section](../../GettingStarted/BuildInstructions/CarbonFiberPrep.md){: .btn}
[Next Section](../../GettingStarted/BuildInstructions/LandingGear.md){: .btn .float-right}

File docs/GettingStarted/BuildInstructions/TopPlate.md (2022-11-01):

---
layout: default
title: "3. Top Plate"
parent: Build Instructions
nav_order: 4
---

# Top Plate of the Central Hub
{: .no_toc }
The central hub is made up of three different plates each housing different electronics. The focus here is on the top plate and mounting the components which are unlikely to be removed.

## Table of Content:
{: .no_toc .text-delta }

1. TOC
{:toc}

## Requirements: 

### Parts:

| Component | Quantity | Description |
|:---|:---|:---|
| [Oblong Top Plate](https://github.com/landrs-toolkit/LANDRs-Science-Drone/tree/main/Design/MechanicalDesign/CenterHubs/TopPlate) | 1 | CNC'd carbon fiber plate |
| Cube Orange | 1| CubePilot flight controller and standard board |
| [Top Rail Mount](https://github.com/landrs-toolkit/LANDRs-Science-Drone/tree/main/Design/MechanicalDesign/RailMounting) | 4 | 3D Printed top rail mount |
| Gimbal Rails | 2 | 12x10x250mm carbon fiber tube|
| M2.5 x 8mm screw | 4| M2.5 screw to secure the flight controller|
| M3 x 8mm bolt | 12 | M3 hex socket bolts for gimbal mounts|

*Note: It's suggested to print two of the top gimbal mounts in one filament colour and the remain two in another colour. This assists with identifying orientation of the HexaQuad.*

## Assembling the Oblong Top Plate:
The following illustration will assist with mounting the components that go on the top plate. The top plate is the same for both configurations of the HexaQuad.

CFTube

### Step 1: *Attaching the flight controller*

The top plate is symmetrical and thus the flight controller can be mounted facing either direction. Once a direction is chosen it is best to stick with it. There is an indicator arrow on the top of the Orange Cube indicating the forward direction.

CFTube

The flight controller is secured to the top plate with **4 x M2.5x8mm** screws. The mounting holes are illustrated above.

### Step 2: *Mounting the rail mounts*
There are four rail mounts located on the top plate. Each one is fixed to the top plate by **2 x M3x8mm** hex socket bolts. The rail mounts should be orientated with the hole to secure the rail facing out from the center of the plate.

**FIX THE IMAGE!**

CFTube

**4 x M3x8mm** hex socket bolts can be threaded into the part of the rail mounts that secure the rail. This is highlighted in the detailed view by the green arrows.

### Step 3: *Securing the gimbal rails*
The two carbon fiber gimbal rails (**12x10x250mm**) can now be secured in the rail mounts. Slide the rails through the eye of the mounts, the end of the tube should be **40mm** from the end of the rail mount as shown below.

CFTube

The rail is secured in place by tightening the four bolts in the side of the rail mounts. **DO NOT** over tighten these bolts as it will break through the 3D prints.

### Step 4: *Mounting the GPS stand*
The GPS mount was designed to snap fit onto one of the rail mounts. Thus, it does not require any bolts to secure it.

CFTube

The GPS should be mounted at the front of the HexaQuad as illustrated below. It is mounted at the front to isolate it from the power systems interference which is located at the back of the HexaQuad.

[Previous Section](../../GettingStarted/BuildInstructions/Rotorbooms.md){: .btn} [Next Section](../../GettingStarted/BuildInstructions/BatPlate.md){: .btn .float-right}

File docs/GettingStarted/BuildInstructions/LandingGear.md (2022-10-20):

---
layout: default
title: "1. Landing Gear"
parent: Build Instructions
nav_order: 2
---

# Landing Gear
{: .no_toc }
We start our assembly with the landing gear. These are simple structures and can be assembled almost completely before being added to the rest of the frame. The landing gear of the HexaQuad is extremely simple and was designed as such to be easy to replace and avoid breaking in the case of a crash.

## Table of Content:
{: .no_toc .text-delta }

1. TOC
{:toc}

## Requirements: 

### Parts:

| Component | Hex Quantity | Quad Quantity | Description |
|:---|:---|:---|:---|
| [Landing Gear Tube Cap](https://github.com/landrs-toolkit/LANDRs-Science-Drone/tree/main/Design/MechanicalDesign/LandingGear) | 3 | 4 | Foot of landing gear |
| Carbon Leg | 3 | 4 | 25x23x350mm length of carbon tube |
| [Bottom Rotorboom Mount](https://github.com/landrs-toolkit/LANDRs-Science-Drone/tree/main/Design/MechanicalDesign/RotorBoomMounts/NutInsert) | 3 | 4 | Landing gear mount to connect to hub |
| M3 30mm bolt | 6 | 8 | M3 socket head 30mm bolt |
| M3 standard Nut | 6 | 8 | M3 standard nut for 3D prints |

## Assembling the Landing gear:

The following illustrations will assist with assembling the landing gear of the HexaQuad. Repeat the following steps 3 times for Hex or 4 times in the case of the Quad configuration.

CFTube

### Step 1: *Fit the landing gear tube cap*

Slide the landing gear tube cap into the lower end of the carbon fiber tube. The lower end is identified by a securing hole located 10mm from the end of the tube.

CFTube

### Step 2: *Fit the rotorboom bottom mount*

The rotorboom bottom mount slides onto the top end of the carbon fiber tube. The top end of the carbon fiber tube is identified by a securing hole located 20mm from the end of the tube.

### Step 3: *Secure the prints with M3 bolts*

Taking two **M3x30mm** hex socket bolts, align the holes and thread the bolts through. 

*Incase the bolts are loose, rather use M3x35mm and a standard M3 nut to secure the tube cap and rotorboom mount.*

[Previous Section](../../GettingStarted/BuildInstructions/PrepWork.md){: .btn} [Next Section](../../GettingStarted/BuildInstructions/Rotorbooms.md){: .btn .float-right}

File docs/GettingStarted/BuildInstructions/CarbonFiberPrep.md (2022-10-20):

---
layout: default
title: Cutting Carbon Fiber
parent: Preparation
grand_parent: Build Instructions
nav_order: 1
---

# Carbon Fiber Tube Preparation:
We need to prepare carbon fiber tubes for use in the landing gear and for the gimbal rails. This involves cutting the tubes to the correct lengths and drilling holes to thread bolts.

**Required Tools:**

| Tool | Description |
|:---|:---|
|Drill press |To make straight holes in the carbon fiber tubes|
|M3 Drill bit |Drill bit for an M3 hole, no tapping required|
|Hole guide |Assists with making holes directly opposite each other|
|Hacksaw |To cut the tubes to length|
|Tape |Any kind, assists with making a straight cut|
|Measuring  |Tape measure and vernier caliper|
|Pencil  |To mark components for cutting|

**Materials:**

| Item | Quantity | Dimensions (IDxODxLen) |
|:---|:---|:---|
| Landing Gear Legs |3 (*Hex*) or 4 (*Quad*) | 23x25x500mm|
| Gimbal Rails |2 | 10x12x500mm|

## Landing Gear Legs:
At the end of this task you will have carbon fiber tubes which can be used in the landing gear.

To Do:
- Cut the standard lengths of carbon fiber tube to be 350mm
- Drill holes on either end of the tube to secure it to the foot and rotorboom mount.

### Legs Cutting:
Use: 23x25x500mm Carbon Fiber Tubes

Final result: 3-4x (23x25x350mm)

**Note: take care when cutting carbon fiber, as the small particles should not be inhaled!**

1. Measure and mark a 350mm length on the carbon fiber tube.

2. Using the tape, cut a piece long enough to go around the circumference of the tube. 
    - Carefully align the tape with the mark, wrapping the tape around the tube. 
    - When wrapping the tape around the tube, make sure the edges line up and there is no overhang.
3. Using the Hacksaw, cut along the tape edge aligned with the 350mm mark.
4. Repeat steps 1-3 for the total number of landing gear legs you require. (*3 for Hex and 4 for Quad*)

### Drilling Holes:

There are two holes to be drilled on each landing gear leg. The holes are located on either end of the tube.

1. From the end of the tube measure 10mm towards the center of the tube and mark with a pencil.
2. Using the hole guide, located the mark in the eye of the guide.
3. Secure the guide and tube so that they cannot move. Then align the mark with the drill bit on the drill press.
4. Make the hole using the drill press and M3 bit. 
5. On the opposite end of the tube, measure 20mm in and mark with a pencil.
6. Steps 2-3 can then be repeated for the mark located 20mm in from the end.
7. All the steps above can then be repeated for all the landing gear legs.

## Gimbal Rails
### Rails Cutting
Use: 10x12x500mm Carbon Fiber Tubes

Final result: 4x (10x12x250mm) 

**Note: take care when cutting carbon fiber, as the small particles should not be inhaled!**

The process is the same as outlined for the cutting of the landing gear legs. The only difference is the final length should be **250mm**.

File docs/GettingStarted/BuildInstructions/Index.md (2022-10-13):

---
layout: default
title: Build Instructions
nav_order: 2
has_children: true
description: "Step by step information to assist with the assembly of the Nyala HexaQuad"
permalink: /docs/GettingStarted/BuildInstructions
---

# Build Instructions:
This is a step by step guide to assist with the assembly of the Nyala HexaQuad in either of its configurations. This is a general guide and specifics relating to either configuration will be made known when required.
{: .fs-6 .fw-300 }

## Using the Build Instructions
*Outline how someone should use these docs.*
1. Start with the preparation tasks
    1. Cut carbon fiber sheets and tubes
    2. Acquire all parts
    3. Print all the parts
    4. Eletrical Work
2. Start Assembly
    1. Assemble it, incorporating electronics at necessary levels.
3. Proceed to Preflight setup

## Glossary of Terms

| Short Hand | Meaning |
|:---|:---|
|BOM |Bill of Materials|
|ID |Inner Diameter|
|OD |Outer Diameter|
|Len |Length|

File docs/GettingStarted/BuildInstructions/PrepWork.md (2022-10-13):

---
layout: default
title: Preparation
parent: Build Instructions
has_children: true
nav_order: 1
---

# Preparation for Assembly
{: .no_toc }
There are a number of task that must be complete before assembly can begin. This doc will outline the tasks to complete to make the assembly process efficient.
{: .fs-6 .fw-300 }

## Table of Content:
{: .no_toc .text-delta }

1. TOC
{:toc}

# Carbon Fiber Cutting:

**NOTE: *Cutting carbon fiber produces small particles which can be dangerous for your health. Avoid inhaling these particles!***

The HexaQuad uses custom cut carbon fiber sheets for the central hub plates and standard tubes for the rotorbooms, landing gear and gimbal rails.

**Central Plates:**

The central hub plates require precision cutting with a CNC routing setup. It is best to consult a professional for this unless you have experience.

**Standard Tubes:**

Some of the carbon fiber tubes require cutting to specific lengths as well as drilling holes to assist with connection to 3D printed parts. Fortunately, this is a simple task and can be complete in a basically equiped workshop.

Guidance on cutting the tubes and drilling holes can be found here:

[Cutting Carbon Fiber Tubes](../../GettingStarted/BuildInstructions/CarbonFiberPrep.md){: .btn}

## Carbon Fiber Parts:

| Part Name | Quad Quantity | Hex Quantity |Dimensions|Cutting Type|
|---|---|---|----|---|
|[BatteryPlate](https://github.com/landrs-toolkit/LANDRs-Science-Drone/tree/main/Design/MechanicalDesign/BatteryPlate) | 1 | 1| 3mm thick|CNC|
| [CenterHub Top](https://github.com/landrs-toolkit/LANDRs-Science-Drone/tree/main/Design/MechanicalDesign/CenterHubs/TopPlate)  | 1 | 1|3mm thick|CNC|
| [CenterHub Bot](https://github.com/landrs-toolkit/LANDRs-Science-Drone/tree/main/Design/MechanicalDesign/CenterHubs/BottomPlate) | 1 | 1|3mm thick|CNC|
|Landing Gear |4 |3 | 25x23x350mm|Hacksaw|
|Rotorbooms |4 |6 | 25x23x500mm|-|
|Gimbal Rails |4 |4 | 12x10x250mm|Hacksaw|

# 3D Printing Preparation:
There are a number of parts that need to be 3D printed, each having a predetermined print orientation and some requiring nut inserts.

## 3D Printed Parts:
The following is a list of parts that need to be printed:

| Part Name | Quad Quantity | Hex Quantity |
|---|---|---|
|[WingNutExtender](https://github.com/landrs-toolkit/LANDRs-Science-Drone/tree/main/Design/MechanicalDesign/BatteryPlate) | 4 | 4|
| [LandingGearTubeCap](https://github.com/landrs-toolkit/LANDRs-Science-Drone/tree/main/Design/MechanicalDesign/LandingGear)  | 4 | 3|
| [RotorBoomMounts Top](https://github.com/landrs-toolkit/LANDRs-Science-Drone/tree/main/Design/MechanicalDesign/RotorBoomMounts) | 4 | 9|
| [RotorBoomMounts Bot](https://github.com/landrs-toolkit/LANDRs-Science-Drone/tree/main/Design/MechanicalDesign/RotorBoomMounts/NutInsert) | 4 | 3|
| [MotorMounts](https://github.com/landrs-toolkit/LANDRs-Science-Drone/tree/main/Design/MechanicalDesign/MotorMounts) | 4 | 6 |
| [TopRail](https://github.com/landrs-toolkit/LANDRs-Science-Drone/tree/main/Design/MechanicalDesign/RailMounting) | 4 | 4 |
| [BottomRail](https://github.com/landrs-toolkit/LANDRs-Science-Drone/tree/main/Design/MechanicalDesign/RailMounting) | 4 | 4 |
| [GPSMount](https://github.com/landrs-toolkit/LANDRs-Science-Drone/tree/main/Design/MechanicalDesign/GPSMounts) | 1 | 1|
| [PDBMount](https://github.com/landrs-toolkit/LANDRs-Science-Drone/tree/main/Design/MechanicalDesign/PDBMount) | 1 | 1 |
| [NiTubeMounting](https://github.com/landrs-toolkit/LANDRs-Science-Drone/tree/main/Design/MechanicalDesign/SensorMounts/NiTubeMounting) | 2 |2  |
| [RC Receiver](https://github.com/landrs-toolkit/LANDRs-Science-Drone/tree/main/Design/MechanicalDesign/RadioReceivers) | 1 | 1 |
| [Telemetry Radio](https://github.com/landrs-toolkit/LANDRs-Science-Drone/tree/main/Design/MechanicalDesign/RadioReceivers) | 1 | 1  |

Consult the print orientation and nut insert guide to assist with how each part should be printed and if the component requires nut inserts.

[Print Orientation and Inserts](../../GettingStarted/BuildInstructions/PrintGuide.md){: .btn}

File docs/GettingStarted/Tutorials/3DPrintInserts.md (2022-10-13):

---
layout: default
title: 3D Print Inserts
parent: Tutorials
nav_order: 1
---

# Adding Inserts to 3D Prints:
{: .no_toc }
3D printing is a great technique for creating complex parts in a short time, however they generally lack mechanical properties like strength or durability. Inserts give prints improved mechanical performance by embedding components like threaded nuts or bearings.

## Table of Content:
{: .no_toc .text-delta }

1. TOC
{:toc}

# Designing 3D Prints with Inserts:
Designing prints with inserts is a simple task if some basic rules are followed. This section outlines some rules to keep in mind.

## Sizing the Cavity:
When designing a 3D print with an insert there must be a cavity to house the insert. It is recommended to over size the cavity by 0.2mm to account for the printer inaccuracy and for ease of insertion.

## Cavity Shape:
The shape of the cavity will depend on the print orientation. The cavity will either be the same shape as the component or slightly altered. We need to consider the orientation because the cavity will be printed from bottom to top. Below is an example of a cavity with an altered cavity.

 

Generally a cavity will have a top and bottom, especially if it is an *altered* cavity. When altering a cavity it is vital to ensure the top opening is the same width as the widest part of the component, otherwise it will be impossible to insert the component.

## Rules to Keep in Mind:
- Know the print orientation **before** creating a cavity.
- The cavity prints from **bottom to top**.
- Ensure the top opening is as **wide as the widest part** of the component.

# How to Embed a Nut in a 3D Print:
The following steps are for a PrusaMini, however there are concepts that can be transferred to other printers.

## Step 1, *Correct Orientation of the Print:*
The cavity for the insert generally has a bottom and a top. The part must be orientated such that the bottom of the cavity is printed first. If the cavity is printed in reverse, you **will not** be able to insert the nut.

Orientation

## Step 2, *Slicing and Adding a Pause: (Prusa Specific)*
Prusa already have great documentation on this and it can be found [here](https://help.prusa3d.com/article/insert-pause-or-custom-g-code-at-layer_120490).

However, simply put if you slide the orange layer slider on the right of the screen a "+" appears. Clicking this gives you the option to add a `Pause`, `Colour Change` or `Custom G-code` at the **current** layer. Select a `Pause`. Note, you can only add a pause if the print has been sliced.

Slider

## Step3, *Choosing the Correct Layer for a Pause*
We only want to insert the nut into the cavity just before the cavity closes. If we insert the nut before this point it will leave a portion of the nut protruding from the cavity and can collide with the extruder. The idea then, is to determine at which layer the cavity closes.

There are two layers you must find to add a successful pause. The Layer that the **cavity closes** and the layer **before** the cavity closes.

**Layer Before Cavity Closes**

Before

**Layer When Cavity Closes**

After

We want to add the pause on the layer **BEFORE** the cavity closes. Add the pause as described in **Step 2**.
You can then slice the print and export the G-code for printing.

Happy Printing!

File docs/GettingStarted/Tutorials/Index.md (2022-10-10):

---
layout: default
title: Tutorials
nav_order: 2
has_children: true
description: "A set of Tutorails that will aid in assembling, manufacturing and altering the Nyala HexaQuad."
permalink: /docs/GettingStarted/Tutorials
---

# Tutorials:
There are a number of tutorials to assist with the assembly, manufacturing and contruction of the Nyala HexaQuad. Tutorials will focus on specific "How to" tasks
as opposed to the step by step guide on suggested assembly. That can be found in the [building steps](/docs/GettingStarted/BuildInstructions).
{: .fs-6 .fw-300 }

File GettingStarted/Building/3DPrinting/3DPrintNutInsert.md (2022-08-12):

# Adding Inserts to 3D Prints:
Adding items into the 3D prints can be extremely useful and often simplify designs.
It has become quite a common task to embed bearings or nuts into 3D prints. Reason being, it allows complex parts to be created through 3D printing but at the same time provided superior mechanical performance compared to 3D printed equivalents.

## Design of the 3D Print:
Coming Soon... Basically, you have to create a cavity you can slip the nut or bearing into. The cavity must be large enough to house the component in its entirety, otherwise it make contact with the head of printer. Sometimes the cavity can be the shape of the component but this is usually influenced by the print orientation.

DCavity

# Embedding a Nut in a 3D Print:
The following steps are for a PrusaMini, however there are concepts that can be transferred to other printers.

## Step 1, Correct Orientation of the Print:
Ensure the part is oriented on the print plate such that a pause can be added to insert a nut into the cavity. If the cavity is printed in reverse, you **will not** be able to insert the nut.

Orientation

## Step 2, Slicing and Adding a Pause: (Prusa Specific)
Prusa already have great documentation on this and it can be found [here](https://help.prusa3d.com/article/insert-pause-or-custom-g-code-at-layer_120490).

However, simply put if you slide the orange layer slider on the right of the screen a "+" appears. Clicking this gives you the option to add a `Pause`, `Colour Change` or `Custom G-code` at the **current** layer. We desire a simple `Pause` only.

Slider

## Step3, Choosing the Correct Layer for a Pause
We only want to insert the nut into the cavity just before the cavity closes. If we insert the nut before this point it will leave a portion of the nut protruding from the cavity and can collide with the extruder. The idea then, is to determine at which layer the cavity closes.

There are two layers you must find to add a successful pause. The Layer that the **cavity closes** and the layer **before** the cavity closes.

**Layer When Cavity Closes**

After

**Layer Before Cavity Closes**

Before

We want to add the pause on the layer **BEFORE** the cavity closes. On the layer before the cavity closes, add the pause as described in **Step 2**.
You can then slice the print and export the G-code for printing.

Happy Printing!

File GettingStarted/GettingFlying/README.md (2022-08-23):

# Getting Flying with your HexaQuad
A tricky part about building and designing your own sUAS is making sure it is stable and predictable in flight. Beyond ensuring your HexaQuad is constructed correctly we need to ensure it tuned correctly to achieve stablility in flight.

We have been through these steps already and have completed the [tuning guide](https://ardupilot.org/copter/docs/common-tuning.html) according to the Ardupilot documentation. You simply need to upload either the Hex or Quad parameter files to you CubePilot for your respective configuration of the HexaQuad.

## Hexacopter Tuned Parameters:
Parameter file for the Hex configuration of the HexaQuad, [here](https://github.com/landrs-toolkit/LANDRs-Science-Drone/tree/main/GettingStarted/GettingFlying/HexTune).

## Quadcopter Tuned Parameters:
Parameter file for the Quad configuration of the HexaQuad, [here](https://github.com/landrs-toolkit/LANDRs-Science-Drone/tree/main/GettingStarted/GettingFlying/QuadTune).

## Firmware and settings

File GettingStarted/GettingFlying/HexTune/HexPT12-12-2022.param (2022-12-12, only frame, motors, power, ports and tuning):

ATC_ANG_LIM_TC,1
ATC_ANG_PIT_P,15.87652
ATC_ANG_RLL_P,13.71474
ATC_ANG_YAW_P,5.196289
ATC_ANGLE_BOOST,1
ATC_RAT_PIT_D,0.00619467
ATC_RAT_PIT_FF,0
ATC_RAT_PIT_FLTD,11
ATC_RAT_PIT_FLTE,0
ATC_RAT_PIT_FLTT,11
ATC_RAT_PIT_I,0.1128843
ATC_RAT_PIT_IMAX,0.5
ATC_RAT_PIT_P,0.1128843
ATC_RAT_PIT_SMAX,0
ATC_RAT_RLL_D,0.009202571
ATC_RAT_RLL_FF,0
ATC_RAT_RLL_FLTD,11
ATC_RAT_RLL_FLTE,0
ATC_RAT_RLL_FLTT,11
ATC_RAT_RLL_I,0.1925878
ATC_RAT_RLL_IMAX,0.5
ATC_RAT_RLL_P,0.1925878
ATC_RAT_RLL_SMAX,0
ATC_RAT_YAW_D,0
ATC_RAT_YAW_FF,0
ATC_RAT_YAW_FLTD,0
ATC_RAT_YAW_FLTE,1
ATC_RAT_YAW_FLTT,11
ATC_RAT_YAW_I,0.05656004
ATC_RAT_YAW_IMAX,0.5
ATC_RAT_YAW_P,0.5656004
ATC_RAT_YAW_SMAX,0
ATC_RATE_FF_ENAB,1
ATC_RATE_P_MAX,0
ATC_RATE_R_MAX,0
ATC_RATE_Y_MAX,0
BATT_AMP_OFFSET,0
BATT_AMP_PERVLT,60.94627
BATT_ARM_MAH,0
BATT_ARM_VOLT,11
BATT_CAPACITY,8000
BATT_CRT_MAH,2400
BATT_CRT_VOLT,21
BATT_CURR_PIN,15
BATT_FS_CRT_ACT,1
BATT_FS_LOW_ACT,2
BATT_FS_VOLTSRC,1
BATT_LOW_MAH,2600
BATT_LOW_TIMER,10
BATT_LOW_VOLT,21.6
BATT_MONITOR,4
BATT_OPTIONS,0
BATT_SERIAL_NUM,-1
BATT_VLT_OFFSET,0
BATT_VOLT_MULT,19.01298
BATT_VOLT_PIN,14
BATT2_MONITOR,0
BATT3_MONITOR,0
BATT4_MONITOR,0
BATT5_MONITOR,0
BATT6_MONITOR,0
BATT7_MONITOR,0
BATT8_MONITOR,0
BATT9_MONITOR,0
FLTMODE_CH,5
FLTMODE1,0
FLTMODE2,2
FLTMODE3,5
FLTMODE4,3
FLTMODE5,5
FLTMODE6,6
FRAME_CLASS,2
FRAME_TYPE,1
INS_GYRO_FILTER,22
INS_HNTCH_ENABLE,0
MOT_BAT_CURR_MAX,0
MOT_BAT_CURR_TC,5
MOT_BAT_IDX,0
MOT_BAT_VOLT_MAX,25.2
MOT_BAT_VOLT_MIN,19.8
MOT_BOOST_SCALE,0
MOT_HOVER_LEARN,2
MOT_PWM_MAX,1940
MOT_PWM_MIN,1100
MOT_PWM_TYPE,0
MOT_SAFE_DISARM,0
MOT_SAFE_TIME,1
MOT_SLEW_DN_TIME,0
MOT_SLEW_UP_TIME,0
MOT_SPIN_ARM,0.1
MOT_SPIN_MAX,0.95
MOT_SPIN_MIN,0.15
MOT_SPOOL_TIME,0.5
MOT_THST_EXPO,0.72
MOT_THST_HOVER,0.125
MOT_YAW_HEADROOM,200
SERIAL0_BAUD,115
SERIAL0_PROTOCOL,2
SERIAL1_BAUD,57
SERIAL1_OPTIONS,0
SERIAL1_PROTOCOL,2
SERIAL2_BAUD,57
SERIAL2_OPTIONS,0
SERIAL2_PROTOCOL,2
SERIAL3_BAUD,38
SERIAL3_OPTIONS,0
SERIAL3_PROTOCOL,5
SERIAL4_BAUD,38
SERIAL4_OPTIONS,0
SERIAL4_PROTOCOL,5
SERIAL5_BAUD,57
SERIAL5_OPTIONS,0
SERIAL5_PROTOCOL,1
SERIAL6_BAUD,115200
SERIAL6_OPTIONS,0
SERIAL6_PROTOCOL,22
SERVO1_FUNCTION,33
SERVO1_MAX,1900
SERVO1_MIN,1100
SERVO1_REVERSED,0
SERVO1_TRIM,1500
SERVO2_FUNCTION,34
SERVO2_MAX,1900
SERVO2_MIN,1100
SERVO2_REVERSED,0
SERVO2_TRIM,1500
SERVO3_FUNCTION,35
SERVO3_MAX,1900
SERVO3_MIN,1100
SERVO3_REVERSED,0
SERVO3_TRIM,1500
SERVO4_FUNCTION,36
SERVO4_MAX,1900
SERVO4_MIN,1100
SERVO4_REVERSED,0
SERVO4_TRIM,1500
SERVO5_FUNCTION,37
SERVO5_MAX,1900
SERVO5_MIN,1100
SERVO5_REVERSED,0
SERVO5_TRIM,1500
SERVO6_FUNCTION,38
SERVO6_MAX,1900
SERVO6_MIN,1100
SERVO6_REVERSED,0
SERVO6_TRIM,1500
SERVO7_FUNCTION,0
SERVO7_MAX,1900
SERVO7_MIN,1100
SERVO7_REVERSED,0
SERVO7_TRIM,1500
SERVO8_FUNCTION,0
SERVO8_MAX,1900
SERVO8_MIN,1100
SERVO8_REVERSED,0
SERVO8_TRIM,1500
SERVO9_FUNCTION,0
SERVO9_MAX,1900
SERVO9_MIN,1100
SERVO9_REVERSED,0
SERVO9_TRIM,1500

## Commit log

2021-08-18 v1 of cube spacer for tarot frame
    [CubeSpacerV1.SLDPRT]
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2021-08-20 Chore: Alu leg CAD files
    [Aluminium foot v1.SLDPRT, Aluminium foot v2.SLDPRT, Aluminium foot v3.SLDPRT]
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2021-08-25 Update: Created platform for AP
    [CubePlatformV1.SLDPRT, CubePlatformV1.STL]
2021-08-25 Update: Added Ribs to CubePlatform for stability
    [CubePlatformV2.STL]
2021-08-27 Update: Simplified CubePlateform to version 3, 3D print ready
    [CubePlatformV3.STL]
2021-08-31 Update: Committed CakeTin 3D Model
    [CakeTinV1.SLDPRT]
2021-08-31 Update: Added all chassis design ideas
    [ChassisClampHex.SLDASM, ChassisClampV1.SLDPRT, ChassisPlateDoDeca.SLDPRT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]
2021-09-07 Update: Create U-Channel Clamp and Assembly
    [ChassisUClampV1.SLDPRT, ChassisUDoDeca.SLDASM]
2021-09-13 TestFrame: RFD mount and Clamp for Arm
    [RFDHousingBot.SLDPRT, RFDHousingTop.SLDPRT, RndArmClampV1.SLDPRT]
2021-09-14 Update: Adjusted hole size of screw to 3D print
    [RndArmClampV1.SLDPRT]
2021-09-15 New: Created the bottom cover for the RFD900x telem radio
    This connects onto the RFD arm clamp. This clamp is an initial attempt at connecting sensors on the legs
    [RFDBotCoverV1.SLDPRT]
2021-09-15 Update: Fixed dimensions with footprint values
    https://fcc.report/FCC-ID/2ADLE-900X/4165637.pdf
    page 9
    [RFDBotCoverV1.SLDPRT]
2021-09-15 Update: Complete RFD top cover and created STL files
    [RFDBotCoverV1.STL, RFDTopCoverV1.SLDPRT, RFDTopCoverV1.STL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]
2021-09-15 Update: folding mast base edited to tarot frame
    [fmBaseTarot2Flanges.stl, fmBaseTarot4Flanges.stl]
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2021-09-17 Chore: cleaned up files
    [RFDBotCoverV1.SLDPRT, RFDBotCoverV1.STL, RFDHousingBot.SLDPRT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]
2021-09-28 Update: Design fixes for 3D printing
    [RFDBotCoverV2.SLDPRT, RFDTopCoverV1.SLDPRT, RFDTopCoverV1.STL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]
2021-10-01 Update: Improved GPS mount and added SCAD files
    [fmBaseTarot12Flanges.stl, folding_mast.scad, mast_lib.scad]
2021-10-01 Update: Fixed sizing of RFD Cover, created STLs
    [RFDBotCoverV2.SLDPRT, RFDBotCoverV2.STL, RFDTopCoverV1.SLDPRT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]
2021-10-04 Update: Fixed hole spacing issue for M5 bolt
    [RndArmClampV1.SLDPRT, RndArmClampV1.STL, RndArmClampV2.SLDPRT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]
2021-10-22 Update: added SW zips files of center hubs
    [ChassisPlateDoDecaMaxSize.SLDPRT]
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2021-10-25 Chore: Trying to version the SW files
    [OblongCenterHub420mm.SLDPRT]
2021-11-19 New: Round Tube Clamps to test with 3D printer
    [3DPClampEnclose.SLDPRT, RndHalfClampTop.SLDPRT]
2021-11-19 Update: fixed top equations and made bot version
    [RndHalfClampBot.SLDPRT, RndHalfClampTop.SLDPRT]
2021-11-19 Fix: small adjustment to equation
    [RndHalfClampBot.SLDPRT]
2021-11-19 Fix: updated sizes and equations
    [RndHalfClampBot.SLDPRT, RndHalfClampTop.SLDPRT]
2021-11-30 New: Landing Gear Solidworks Files, soon to be updated
    [LGLegMountLeft.SLDPRT, LGLegMountRight.SLDPRT, LGTubeAsm.SLDASM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]
2021-12-01 Updates: To readme, CF Leg and Oblong Center Hub
    [CHObDoubleTop.SLDPRT, LGLegMountLeftV2.SLDPRT, LGLegMountRightV2.SLDPRT]
2021-12-02 Update: New Mount design, V3, and file restructure
    [LGLegMountBot.SLDPRT, LGLegMountBot.STL, LGLegMountLeft.SLDPRT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]
2021-12-02 V2 Update:Created STL files
    [LGLegMountLeftV2.STL, LGLegMountRightV2.STL]
2021-12-03 Uploaded Files and update readmes
    [CHDoDeDoubleBot.SLDPRT, CHObDoubleBot.SLDPRT, FrameAsmV1.SLDASM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]
2021-12-07 New: STL files for illustration purposes
    [CHDoDeDoubleBot.STL, CHObDoubleTop.STL, FrameAsmV1.STL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]
2021-12-10 Fix: New solution to the cutting mount holes
    [LGLegMountBotV3.1.SLDPRT, LGLegMountTopV3.1.SLDPRT]
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2022-01-18 Fixed Orientation of STL file
    [FrameHEXAsmV1.STL]
2022-01-20 Battery Mounting plate ideas
    [BatPlateAsm.SLDASM, BatPlateBtFlyNut.SLDPRT, GimbalMtWThread.SLDASM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]
2022-01-20 Simple Battery model for illustration purposes
    [10AhBattery.SLDPRT]
2022-01-20 Battery Plate and Gimbal STL visual
    [BatPlateAsm.STL]
2022-01-24 BackUp: 10mm Tube quick release clamp
    [TubeClampAsm10.SLDASM, TubeClampBot10mm.SLDPRT, TubeClampTop10mm.SLDPRT]
2022-01-24 Update: New position for top rail mount holes
    [CHObDoubleTopV1.2.SLDPRT]
2022-01-27 Update: Enlarged parts, further updates coming
    [TubeClampBot10mm.SLDPRT]
2022-02-01 Update: V3.1 of the Tube Leg Assembly
    [LGTubeAsm.SLDASM]
2022-02-01 Update: Fix for assemblies
    [CFRndRB500mm.SLDPRT]
2022-02-01 Fixing branches
    [CFRndRB500mm.SLDPRT, LGTubeAsm.SLDASM]
2022-02-01 Update: V3.1 of the LG Asm
    [LGTubeAsm.SLDASM]
2022-02-01 Update: V3.1 Rotor mount only
    [RotorMountOnlyAsm.SLDASM]
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2022-02-14 Update: Wire access cutouts
    [CHObDoubleTopV1.2.SLDPRT]
2022-02-22 Update: Prototype 1 Top Plate
    Final design sent for cutting at Flying Robots for Prototype 1
    [CHObDoubleTopV1.2.SLDPRT]
2022-02-22 Update: Bottom Plate for Prototype 1
    Final design sent to Flying Robot to cut for Prototype 1
    [CHDoDeDoubleBotV1.2.SLDPRT]
2022-02-22 Update: Adjusted fitting of 3D prints
    [LGLegMountBotV3.1.SLDPRT, LGLegMountTopV3.1.SLDPRT]
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2022-02-22 New: Proposed 3D Printed Motor Mounts
    [MMPrint.SLDPRT, MMPrintV1.2.SLDPRT]
2022-02-22 Update: Plate for prototype 1
    [BatPlateBtFlyNut.SLDPRT]
2022-03-22 Upload: Added DXF files for CF plates
    [BatPlateBtFlyNut.DXF, CHDoDeDoubleBotV1.2.DXF, CHObDoubleTopV1.2.DXF]
2022-03-22 Upload: Added MotorMount STL file
    [MMPrintV1.2.STL]
2022-03-22 Upload: STL files for Landing gear v3.1
    [LGTubeCap.STL]
2022-03-23 Update: Adjusted LG Bot part and STL files
    [LGLegMountBotV3.1.SLDPRT, LGLegMountBotV3.1.STL, LGLegMountTopV3.1.STL]
2022-03-24 Init Upload: 3D print specimens for stress tests
    [D638-Type1.SLDDRW, D638-Type1.SLDPRT, D638-Type1.STL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]
2022-06-16 Changed MM, fillet for better strain dist. Resize too
    [MMPrintV1.2.SLDPRT, MMPrintV1.3.SLDPRT]
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2022-06-16 Gps base plate for rail mount
    [HEREGpsBaseP.SLDPRT]
2022-06-16 Inital Commit of top rail mount
    [PrtTopGimbalNutInsert.SLDPRT]
2022-06-17 Resized the Tube hole, was too small to fit
    [LGLegMountBotV3.1.SLDPRT]
2022-06-17 Added a clearance cut for the motor shaft. Currently rubbing
    [MMPrintV1.3.SLDPRT]
2022-06-30 Delete TarotFrame directory
    Not related to new drone
    [GimbalAluORing.SLDPRT, GimbalORingDamper.SLDPRT, GimbalVibDamperAsm.SLDASM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]
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2022-08-19 Fixed Insert Tut 19/08
2022-08-19 New Type-C Mounts, Fixed readmes 19/08
    [C-typeSimpleCase.SLDPRT, C-typeSimpleCase.STL, SimpleCaseBatPMount.SLDPRT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]
2022-08-22 SnapMounts and Type-C files 22/08
    [BotRailSnapMount.SLDPRT, BotRailSnapMount.STL]
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2022-10-12 12/10 PrintOri doc and fixes
2022-10-12 12/08 fix print guide
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2022-10-14 14/08 corrected part
    [MMPrintV1.4.SLDPRT]
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2022-12-07 07/12 Assembly docs and fixed readme
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2023-01-17 17/01 Reinforced Motor mounts
    [MMPrintV1.5.SLDPRT, MMPrintV1.5.STL]
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
